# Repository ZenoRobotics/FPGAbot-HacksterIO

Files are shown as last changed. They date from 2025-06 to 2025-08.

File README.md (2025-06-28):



## FPGAbot-HacksterIO

The FPGA code included here goes with the project writeup I published on Hackster.io at:

https://www.hackster.io/pzeno/rtl-level-fpga-design-of-a-mobile-robot-motor-controller-c3d363

Step by step instructions on how to create this project in AMD Vivado is in the process of being added here.

### Full Parts List

I will be modifying the list below such that you can actually access the links. Here are a few main ones:

1. Adiuvo Spartan-7 and RP2040 board link: https://www.adiuvoengineering.com/product-page/leonidas-spartan-7-rpi-2040
2. DC12V Encoder Gear Motor with Mounting Bracket, 65mm, 130RPM.  https://www.amazon.com/gp/product/B07X7M1LLQ/ref=ppx_yo_dt_b_asin_title_o00_s00?ie=UTF8&psc=1
3. Waxman Caster Wheel, 1 1/4" plate black/gold. https://www.lowes.com/pd/Waxman-1-1-4-in-Plastic-Swivel-Caster/3683910
4. L298N Motor Driver (Qty 2 in this link, but only need 1). https://www.amazon.com/dp/B0DPPWFZ1C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
5. 1 X 12 Position Power Distribution Board 2 Inputs 2 x 13 Outputs for DC AC Voltage. https://www.amazon.com/dp/B07DW2C4ZB?psc=1&smid=AUGR43JJM44E6&ref_=chk_typ_imgToDp
6. Twidec/5Pcs Rocker Switch AC 6A/250V 10A/125V SPST 2 Pins 2 Position ON/Off. https://www.amazon.com/Twidec-Rocker-Position-Pre-soldered-KCD1-1-101/dp/B0B6ZRMQLW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

#### List Image


### 3D Printer STL Files

These files can be found above. 

Power Switch Casing: Housing_for_switch.stl 





RC Enable Switch: RockerSwitchPanel.stl




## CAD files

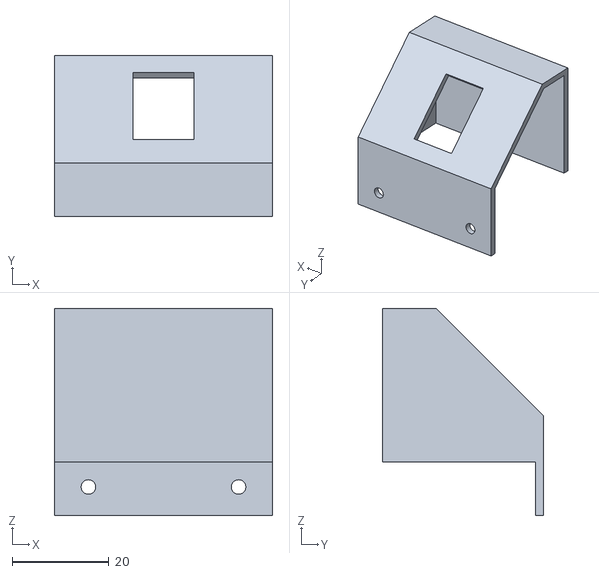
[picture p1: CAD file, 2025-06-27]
3D_Print_STL/Housing_for_switch.STL
45.0 x 33.2 x 42.8

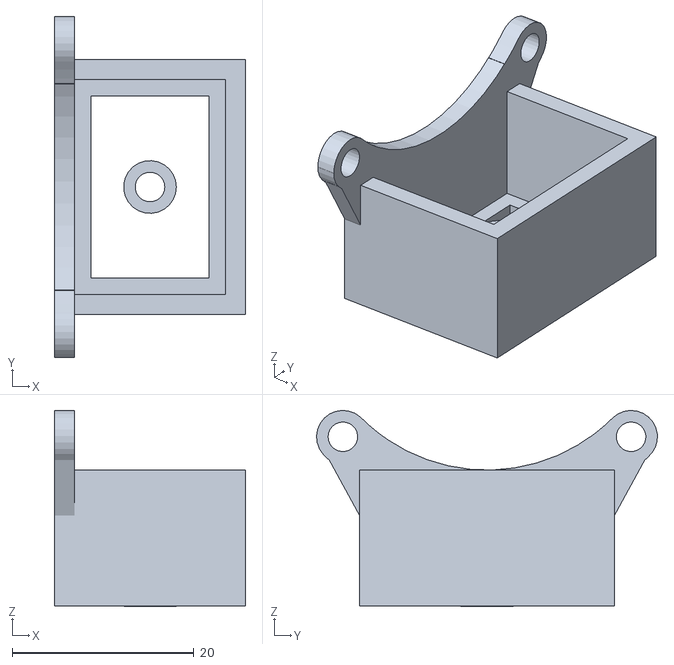
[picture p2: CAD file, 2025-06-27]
3D_Print_STL/RockerSwitchPanel.stl
21.0 x 37.5 x 21.6

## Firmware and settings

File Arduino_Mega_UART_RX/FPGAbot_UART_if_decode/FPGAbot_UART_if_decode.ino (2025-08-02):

#include <stdint.h>

void setup() {
  // Initialize the default Serial port for communication with the computer (Serial Monitor)
  Serial.begin(115200); 
  Serial.println("Serial Monitor Ready!");

  // Initialize Serial1 for communication with an external device
  // Replace 9600 with the desired baud rate for your device
  Serial1.begin(57600); //115200); 
  Serial.println("Serial1 Ready!");
}

byte incomingByte;
byte headerByte;
uint16_t encdr_val;
int byteCnt = 0;

void loop() {
  if (Serial1.available() > 0) { // Check if data is available
    incomingByte = Serial1.read(); // Read the incoming byte
    if ((incomingByte == 0xFD) || (incomingByte == 0xFE)) {
       headerByte = incomingByte;
       if (incomingByte == 0xFD)
          Serial.print("L: "); 
       else
          Serial.print("  R: "); 
       
       while (Serial1.available() == 0) {};
       incomingByte = Serial1.read(); // Read the incoming byte
       encdr_val = incomingByte << 8;
       byteCnt = 1;
       if ((headerByte == 0xFD) && (incomingByte == 0xFD)) {
         Serial.print("    ");
         return;
       }
       else if ((headerByte == 0xFE) && (incomingByte == 0xFE)) {
         Serial.println("");
         return;
       }
         
         
       //Serial.print(incomingByte,HEX); // Print the received byte
       
       while (Serial1.available() == 0) {};
       incomingByte = Serial1.read(); // Read the incoming byte
       encdr_val = encdr_val | incomingByte;
       byteCnt = 2;
       //Serial.print(incomingByte,HEX); // Print the received byte
       //Serial.print("   ");
       //Serial.print(encdr_val,HEX); // Print the received byte

       if (byteCnt == 2) {
         Serial.print(encdr_val,HEX); // Print the received byte
         if (headerByte == 0xFE)
           Serial.println(""); 
       }
       encdr_val = 0;
       incomingByte = 0;
       byteCnt = 0;
          
    }
  }
}

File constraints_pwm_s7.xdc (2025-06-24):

#SYS_CLK External Gen  100MHz Schematic pg. 8/7
set_property PACKAGE_PIN G11 [get_ports clk_100MHz]
set_property IOSTANDARD LVCMOS33 [get_ports clk_100MHz]

set_property PACKAGE_PIN G4 [get_ports rst_n]
set_property IOSTANDARD LVCMOS33 [get_ports rst_n]

#leds 0 thru 3
set_property PACKAGE_PIN E11 [get_ports {led[3]}]
set_property IOSTANDARD LVCMOS33 [get_ports {led[3]}]
set_property PACKAGE_PIN M10 [get_ports {led[2]}]
set_property IOSTANDARD LVCMOS33 [get_ports {led[2]}]
set_property PACKAGE_PIN A10 [get_ports {led[1]}]
set_property IOSTANDARD LVCMOS33 [get_ports {led[1]}]
set_property PACKAGE_PIN D12 [get_ports {led[0]}]
set_property IOSTANDARD LVCMOS33 [get_ports {led[0]}]

#Push Buttons 0 thru 3
set_property PACKAGE_PIN M5 [get_ports {rst}]
set_property IOSTANDARD LVCMOS33 [get_ports {rst}]
#set_property PACKAGE_PIN L5 [get_ports {setpt_latch}]
#set_property IOSTANDARD LVCMOS33 [get_ports {setpt_latch}]
#set_property PACKAGE_PIN N4 [get_ports {btn[2]}]
#set_property IOSTANDARD LVCMOS33 [get_ports {btn[2]}]
#set_property PACKAGE_PIN P5 [get_ports {btn[3]}]
#set_property IOSTANDARD LVCMOS33 [get_ports {btn[3]}]


     
#Switches 0 thru 3
set_property PACKAGE_PIN A12 [get_ports {rc_en}]
set_property IOSTANDARD LVCMOS33 [get_ports {rc_en}]
#set_property PACKAGE_PIN A13 [get_ports {lt}]
#set_property IOSTANDARD LVCMOS33 [get_ports {lt}]
#set_property PACKAGE_PIN B13 [get_ports {rt}]
#set_property IOSTANDARD LVCMOS33 [get_ports {rt}]
#set_property PACKAGE_PIN B14 [get_ports {rc_en}]
#set_property IOSTANDARD LVCMOS33 [get_ports {rc_en}]


#RP2040 Interface     1st 4 Functions:
#RP Port: GPIO0   SPI0 RX    UART0 TX    I2C0 SDA    PWM0 A
set_property PACKAGE_PIN E13 [get_ports uart_rx]
set_property IOSTANDARD LVCMOS33 [get_ports uart_rx]
#RP Port: GPIO1   SPI0 CSn   UART0 RX    I2C0 SCL    PWM0 B
set_property PACKAGE_PIN C14 [get_ports uart_tx]
set_property IOSTANDARD LVCMOS33 [get_ports uart_tx]
#RP Port: GPIO4     UART1 TX    
#set_property PACKAGE_PIN F12 [get_ports uart_rx]
#set_property IOSTANDARD LVCMOS33 [get_ports uart_rx]
#RP Port: GPIO5     UART1 RX    
#set_property PACKAGE_PIN F14 [get_ports uart_tx]
#set_property IOSTANDARD LVCMOS33 [get_ports uart_tx]

#PMOD0
#Pin 1
set_property PACKAGE_PIN H12 [get_ports {in1_l298n_dir}]          
set_property IOSTANDARD LVCMOS33 [get_ports {in1_l298n_dir}]
#Pin 2     
set_property PACKAGE_PIN H11 [get_ports {in2_l298n_dir}]          
set_property IOSTANDARD LVCMOS33 [get_ports {in2_l298n_dir}]
#Pin 3
set_property PACKAGE_PIN H14 [get_ports {encoder_a_m1}]          
set_property IOSTANDARD LVCMOS33 [get_ports {encoder_a_m1}]
#Pin 4
set_property PACKAGE_PIN H13 [get_ports {encoder_b_m1}]          
set_property IOSTANDARD LVCMOS33 [get_ports {encoder_b_m1}]
#Pin 7
set_property PACKAGE_PIN J14 [get_ports {in3_l298n_dir}]          
set_property IOSTANDARD LVCMOS33 [get_ports {in3_l298n_dir}]
#Pin 8
set_property PACKAGE_PIN J13 [get_ports {in4_l298n_dir}]          
set_property IOSTANDARD LVCMOS33 [get_ports {in4_l298n_dir}]
#Pin 9
set_property PACKAGE_PIN J12 [get_ports {encoder_a_m2}]          
set_property IOSTANDARD LVCMOS33 [get_ports {encoder_a_m2}]
#Pin 10
set_property PACKAGE_PIN J11 [get_ports {encoder_b_m2}]          
set_property IOSTANDARD LVCMOS33 [get_ports {encoder_b_m2}]

#PMOD1
#Pin 1
set_property PACKAGE_PIN L13 [get_ports {pwm_l298n_enA}]           
set_property IOSTANDARD LVCMOS33 [get_ports {pwm_l298n_enA}]
#Pin 2
set_property PACKAGE_PIN L12 [get_ports {pwm_l298n_enB}]          
set_property IOSTANDARD LVCMOS33 [get_ports {pwm_l298n_enB}]
#Pin 3 - Debug
#set_property PACKAGE_PIN L14 [get_ports {o_Tx_Done}]       Port looks bad, stays high all the time.
#set_property IOSTANDARD LVCMOS33 [get_ports {o_Tx_Done}]
#Pin 4
set_property PACKAGE_PIN M13 [get_ports {o_Tx_DV}]          
set_property IOSTANDARD LVCMOS33 [get_ports {o_Tx_DV}]
#Pin 7
set_property PACKAGE_PIN K12 [get_ports {uart_tx}]          
set_property IOSTANDARD LVCMOS33 [get_ports {uart_tx}]
#Pin 8
#set_property PACKAGE_PIN K11 [get_ports {pwm_l298n_enB}]          
#set_property IOSTANDARD LVCMOS33 [get_ports {pwm_l298n_enB}]
#Pin 9
#set_property PACKAGE_PIN M12 [get_ports {encoder_a_m2}]          
#set_property IOSTANDARD LVCMOS33 [get_ports {encoder_a_m2}]
#Pin 10
#set_property PACKAGE_PIN M11 [get_ports {encoder_b_m2}]          
#set_property IOSTANDARD LVCMOS33 [get_ports {encoder_b_m2}]
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

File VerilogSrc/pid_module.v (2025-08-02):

`timescale 1ns / 1ps
//////////////////////////////////////////////////////////////////////////////////
// Company: 
// Engineer: 
// 
// Create Date: 05/07/2025 03:55:18 PM
// Design Name: 
// Module Name: pid_module
// Project Name: 
// Target Devices: 
// Tool Versions: 
// Description: 
// 
// Dependencies: 
// 
// Revision:
// Revision 0.01 - File Created
// Additional Comments:
// 
//////////////////////////////////////////////////////////////////////////////////


module pid_module #(parameter SIM = 0)
(
    input         clk,
    input         rst,
    input         startSample,
    input         sampleModeEn,    // pass through usr_setpt to pid_out_setpt for test
    input  [15:0] clk_prescaler,
    input   [7:0] usr_setpt,
    input   [7:0] setpt_in_rc_mod1,
    input   [7:0] setpt_in_rc_mod2,
    input  [23:0] feedback_cnt1, //needs conversion to setpt format - positive only from encoder counter 
    input  [23:0] feedback_cnt2, //needs conversion to setpt format - positive only from encoder counter
    input         wheel_dir_1,   //fwd = 0, rev = 1
    input         wheel_dir_2,   //fwd = 0, rev = 1
    //debug       
    output  [6:0] motor1SpdMod_out,
    output  [6:0] motor2SpdMod_out,
    output        pid_data_rdy,
    //end debug
    output        zero_encoders,  //goes to encoder counters L&R
    output  [7:0] pid_out_setpt1,
    output  [7:0] pid_out_setpt2,
    output  sampleFlag // encoder counters on/off switch for sampleMode
    );
    
    // Local Parameter (constant)
    //++++++++++++++++++++++++++++++++++++++++++++++++++++
    localparam Ki  = 1; //5//3;
    localparam Ke  = 2; //0;
    localparam Kv  = 3; //2//1;
    //++++++++++++++++++++++++++++++++++++++++++++++++++++
    localparam SAMPLE_RUN_LOOPS = 10;  // Sample Time = 10 x clk_prescaler x 1/clk_freq = 1sec
    localparam SETPT_TO_TICS_PER_UNIT_TIME  = 3; // 3 tics/0.1sec/setpt
    localparam MAX_SPEED = 70;
    localparam MIN_SETPT_ALLOWED = 48; // motors don't move well at lesser settings.
    localparam THRESHOLD_DXDT = 12; // make sure motor is moving
    localparam THRESHOLD_DV1V2 = 5;
    localparam DOMINANT_CNT_MAX = 9'h09;
    
    // PID States
    localparam IDLE           = 3'b000;
    localparam CALCULATIONS_1 = 3'b001;
    localparam CALCULATIONS_2 = 3'b010;
    localparam CALCULATIONS_3 = 3'b011;
    localparam CALCULATIONS_4 = 3'b100;
    localparam CALCULATIONS_5 = 3'b101;
    localparam CALCULATIONS_6 = 3'b110;
    localparam SET_NEW_SPDS   = 3'b111;
    
    reg [2:0] curr_state = IDLE;
    
    // Internal signals
    
    reg signed [23:0] motor1SpdMod = 24'sh000000;
    reg signed [23:0] motor2SpdMod = 24'sh000000;
    reg signed [6:0]  control_signal1 = 7'sh00; 
    reg signed [6:0]  control_signal2 = 7'sh00;
    reg signed [23:0] prevMotor1SpdMod_Ki = 24'sh000000;
    reg signed [23:0] prevMotor2SpdMod_Ki = 24'sh000000;
  
    reg  [1:0] prev_direction = 2'b00; 
    
    // Clock divider for sampling rate
    reg [15:0] clk_divider = 0;
    reg pidCalcFlag = 0;
    
    reg sampleStateFlag_r = 0;  // high when and sampleModeEn and startCntPulse_r goes high, else low
    reg startSample_r = 0;
    reg  [3:0] sampleLoopCnt = 4'h0;
    reg  startCntPulse_r = 0;
    
    reg signed [23:0] dxdt_enc1  = 24'sh000000; 
    reg signed [23:0] dxdt_enc2  = 24'sh000000;
    reg signed [23:0] ek_21      = 24'sh000000;
    reg signed [23:0] ek_12      = 24'sh000000;
    reg [23:0] prev_encdr_cnt1   = 24'h000000;
    reg [23:0] prev_encdr_cnt2   = 24'h000000;
    reg signed [23:0] Kvdx1dx2   = 24'sh000000;
    reg signed [23:0] Kvdx2dx1   = 24'sh000000;
    reg signed [23:0] Ke_ek_12    = 24'sh000000;
    reg signed [23:0] Ke_ek_21    = 24'sh000000;
    reg signed [23:0] dx1dx2      = 24'sh000000;
    reg signed [23:0] dx2dx1      = 24'sh000000;
     
    reg  [7:0] pid_out_setpt1_r;
    reg  [7:0] pid_out_setpt2_r;
    reg  [7:0] curr_pid_setpt1_r = 8'h00;
    reg  [7:0] curr_pid_setpt2_r = 8'h00;
    reg  [7:0] sample_setpt1_r;
    reg  [7:0] sample_setpt2_r;
    reg  [9:0] target_delta_tics1 = 10'h000;
    reg  [9:0] target_delta_tics2 = 10'h000;
    reg        zero_encoders_r = 1'b0;
    reg        keep_curr_pid_setpts_flag = 0;
    
    reg        dominant_motor = 0;
    reg  [7:0] dominant_motor0_count = 8'h00;
    reg  [7:0] dominant_motor1_count = 8'h00;
    reg  [8:0] dominant_motor_sample_count = 9'h000;
    reg        dominant_motor_found = 1'b0;
    
    wire [23:0] feedback_cnt1_w;
    wire [23:0] feedback_cnt2_w;
    
    reg   pid_data_rdy_r = 1'b0;
    
    assign sampleFlag = sampleStateFlag_r;
    //assign zero_encoders = zero_encoders_r;
    
    assign pid_out_setpt1 = (sampleModeEn == 1) ? sample_setpt1_r : pid_out_setpt1_r; 
    assign pid_out_setpt2 = (sampleModeEn == 1) ? sample_setpt2_r : pid_out_setpt2_r;
    assign motor1SpdMod_out = motor1SpdMod[6:0];
    assign motor2SpdMod_out = motor2SpdMod[6:0];
    
    assign feedback_cnt1_w = (SIM == 0) ? feedback_cnt1 : feedback_cnt1*10;
    assign feedback_cnt2_w = (SIM == 0) ? feedback_cnt2 : feedback_cnt2*10;
    
    assign pid_data_rdy = pid_data_rdy_r;
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

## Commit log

2025-06-24 Pin Constraints File
2025-06-27 Added 3D Printer STL files for switches (optional).
    [Housing_for_switch.STL, RockerSwitchPanel.stl]
2025-08-02 Updates to add UART TX and Use lower RPM Motor
    Previous version was tuned to 500 rpm 12V DC encoder motors. This update is for the more likely used (or similar) 130 rpm version.
    Started adding debug data transmit of debug data out of an instantiated UART Tx Module in the FPGA.
